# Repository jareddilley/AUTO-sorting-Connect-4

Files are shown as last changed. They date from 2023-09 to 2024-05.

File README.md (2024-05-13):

# AUTO-Sorting-Connect-4
[Arduino Blog](https://blog.arduino.cc/2023/09/27/automating-connect-four-setup-and-cleanup/?queryID=undefined)



Fully 3D printed Connect 4 add-on that sorts the pieces for you at the touch of a button.
The solution is made up of 3 parts which will be broken down below: sensing color, dividing pieces, and one-row handling.

Attached is the Fusion 360 so the models can be edited directly and used to better understand how it is broken down. A YouTube link for the build process and comedic relief: https://www.youtube.com/watch?v=7tsY3SJziWs&t=1s

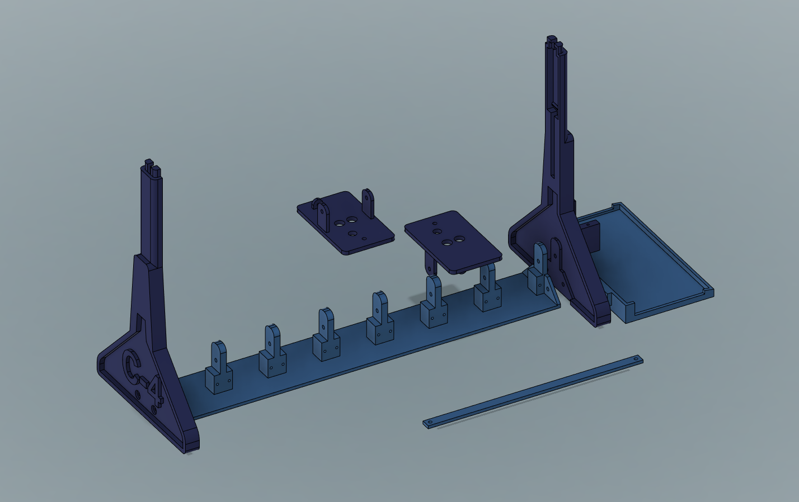
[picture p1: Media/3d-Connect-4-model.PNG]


Below is the full Arduino schematic for anyone trying to build the project. For those who want a closer look, the diagram can be found in the Fritzing Schematic folder. If there are any confusions feel free to ask in the discussion. (don't forget to leave slack in the wires for the platform of the lever to go all the way up and down)

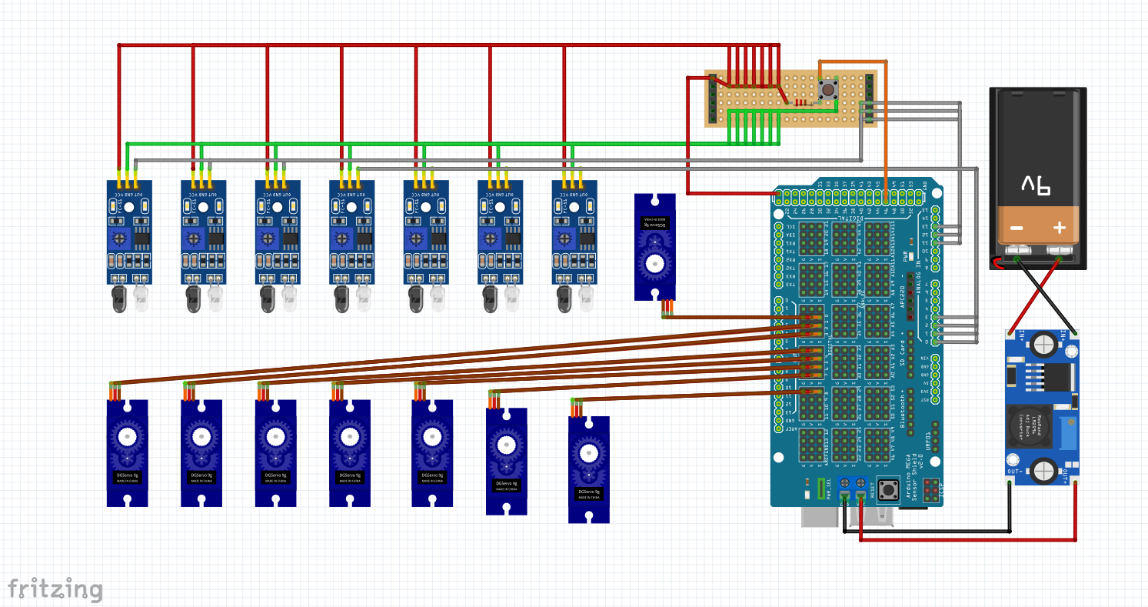
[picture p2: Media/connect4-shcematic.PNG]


# Sensing Color


The IR sensor is able to reflect and receive off of the red piece but not the black piece allowing for a simple binary approach. This requires that one of the piece colors be black, but this method reduces the number of cables and is the simple solution. The most compact place for the sensors, which also does not block the view of the gameplay, ends up being the bottom; we can combine them with the levers that push the pieces to one side or the other.

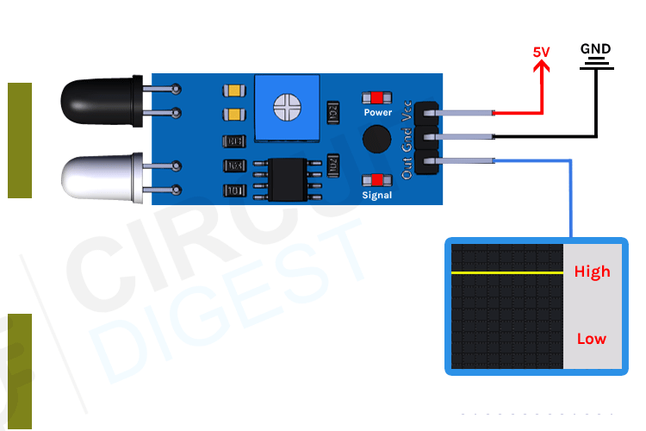
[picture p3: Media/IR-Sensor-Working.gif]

# Dividing Peices


A lever system (think seesaw) is used to push the pieces to one side or the other. A server with a simple linkage is used to tilt the single-point mounted platform to one side or the other letting gravity do the rest. This system is not the most robust approach and has its flaws but is a solution to the problem and can be improved upon. The platform must stop in the middle of each row drop to sense the color before picking a side.
# One Row Handling
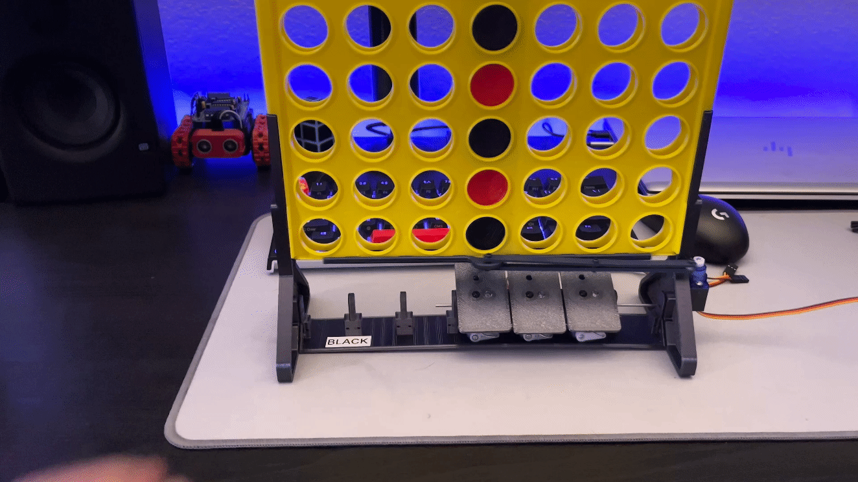
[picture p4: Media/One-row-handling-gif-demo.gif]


The pieces traditionally come out of the bottom so we can use the existing slider to drop the pieces one at a time using a precise servo. The servo can be mounted to the side support and can provide an action that is quick and precise enough to consistently only drop one row at a time. This works under the load of one row or all six.

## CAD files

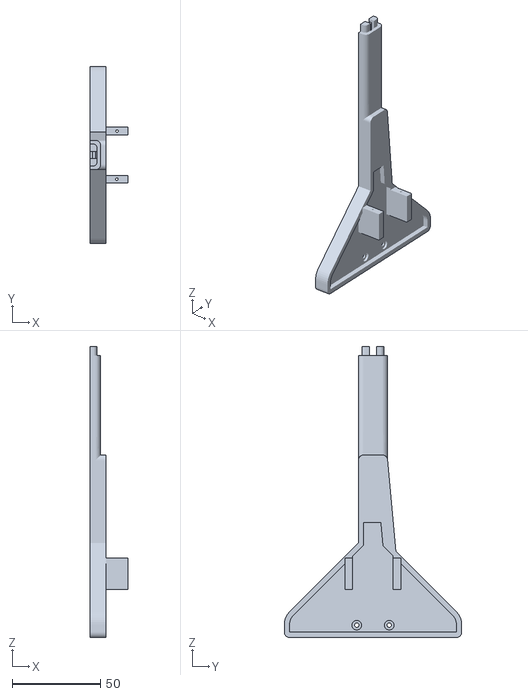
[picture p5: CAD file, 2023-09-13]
STL files/servo_side_support.stl
21.6 x 100.6 x 165.0

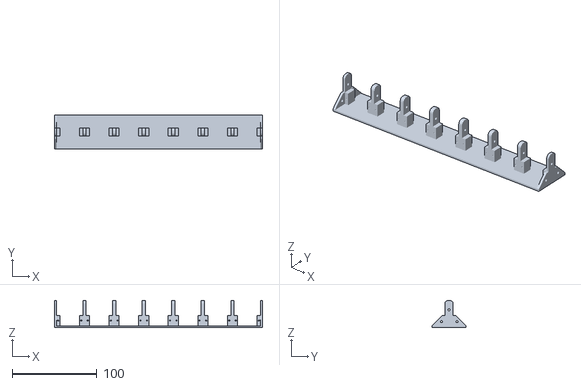
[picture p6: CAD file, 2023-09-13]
STL files/base_X7.stl
246.0 x 40.0 x 32.0

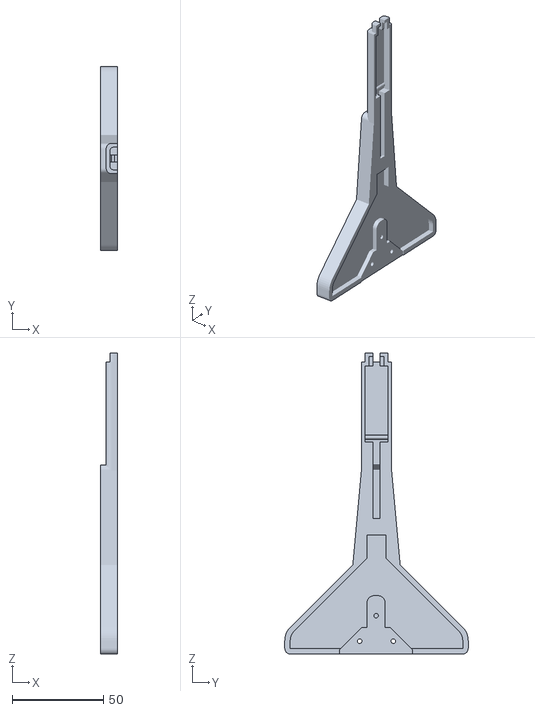
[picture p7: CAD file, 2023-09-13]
STL files/side_support.stl
9.10 x 100.6 x 165.0

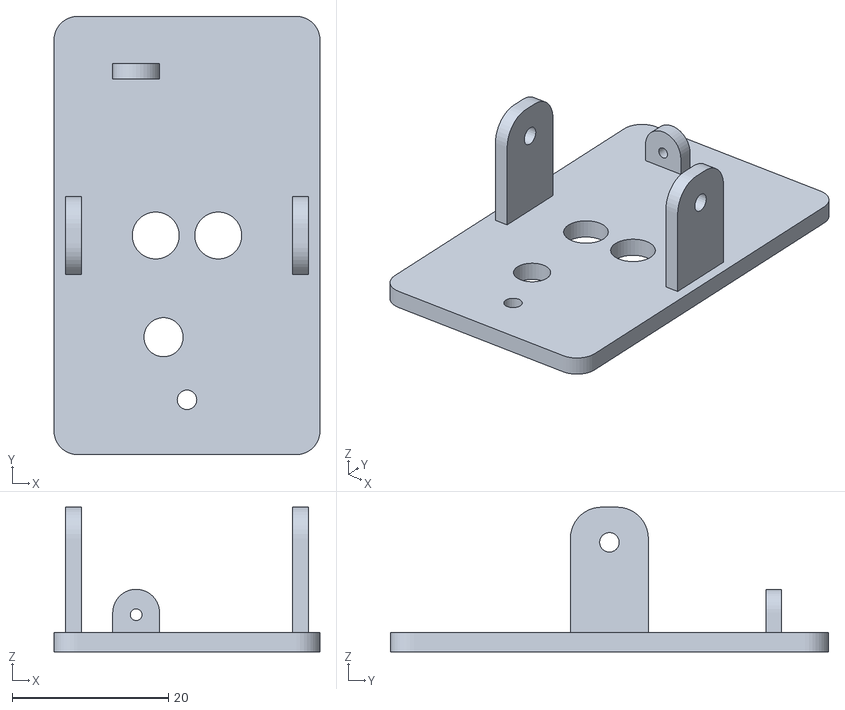
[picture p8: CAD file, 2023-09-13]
STL files/tilt_platform.stl
34.0 x 56.0 x 18.5

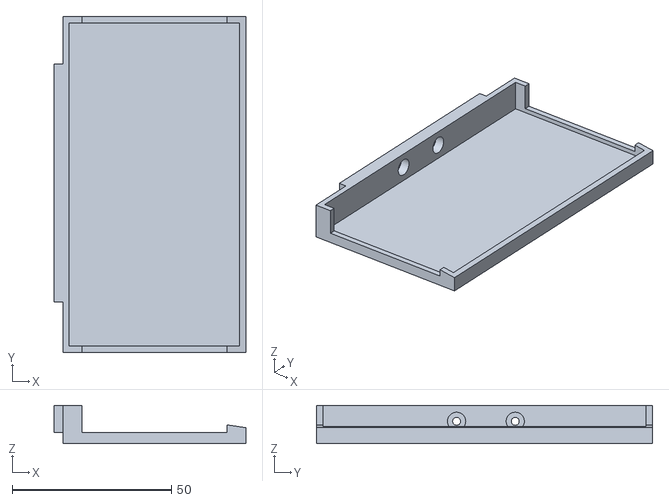
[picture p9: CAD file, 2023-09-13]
STL files/circuit_box.stl
60.2 x 105.5 x 12.0

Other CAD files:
Fusion 360/Sorting Connect 4 Fusion 360.f3d

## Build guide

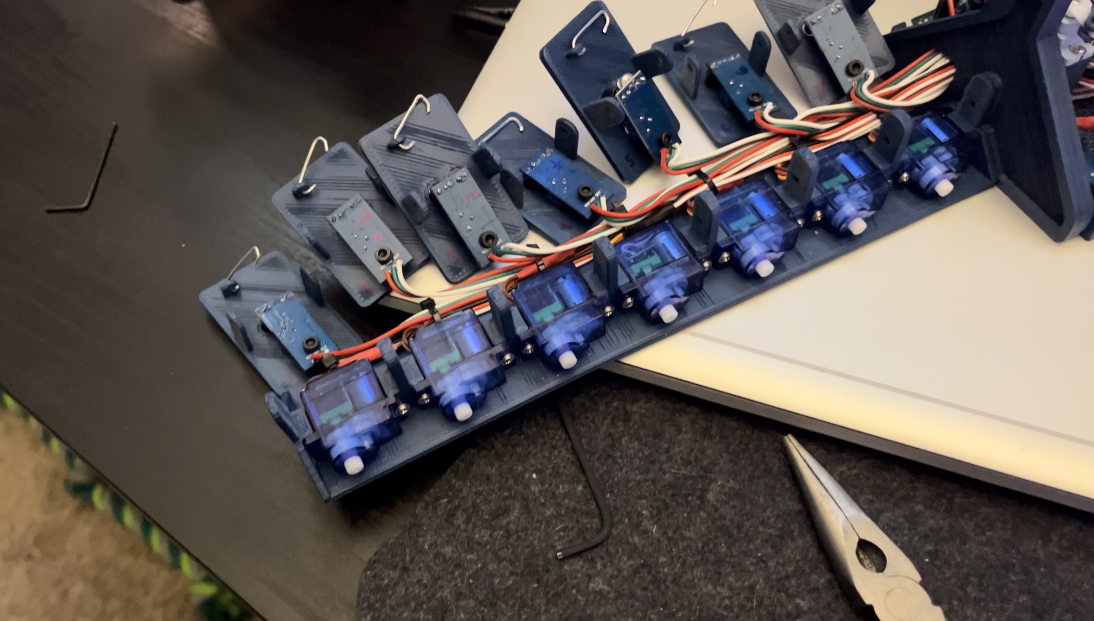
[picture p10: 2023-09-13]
Media/Disassembled-view.jpg

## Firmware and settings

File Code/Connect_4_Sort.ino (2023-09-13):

#include <Wire.h>
#include <Adafruit_PWMServoDriver.h>

// called this way, it uses the default address 0x40
Adafruit_PWMServoDriver pwm = Adafruit_PWMServoDriver();

#define SERVOMIN  100 // this is the 'minimum' pulse length count (out of 4096) 0 degrees
#define SERVOMAX  350 // this is the 'maximum' pulse length count (out of 4096) 90 degrees
#define SERVOMID1  170 // adjustable middle angle
#define SERVOMID2  167
#define SERVOMID3  160
#define SERVOMID4  160
#define SERVOMID5  160 
#define SERVOMID6  180
#define SERVOMID7  180

#define dropServo 0
#define tiltServo1 1 // farthest servo
#define tiltServo2 2
#define tiltServo3 3
#define tiltServo4 4
#define tiltServo5 5
#define tiltServo6 6
#define tiltServo7 7

#define LED_PIN_1 9
#define LED_PIN_2 10
#define buttonPin 46

int currentState = 0;

void setup() {
  pwm.begin();
  pinMode(buttonPin, INPUT);  // set up button pin
  //pinMode(LED_PIN_1, OUTPUT); // set up LED pins
  //pinMode(LED_PIN_2, OUTPUT);
  pwm.setPWMFreq(60);  // Analog servos run at ~60 Hz updates
  pwm.setPWM(tiltServo1, 0, SERVOMID1); // Set Tilt servos to middle
  pwm.setPWM(tiltServo2, 0, SERVOMID2);
  pwm.setPWM(tiltServo3, 0, SERVOMID3);
  pwm.setPWM(tiltServo4, 0, SERVOMID4);
  pwm.setPWM(tiltServo5, 0, SERVOMID5);
  pwm.setPWM(tiltServo6, 0, SERVOMID6);
  pwm.setPWM(tiltServo7, 0, SERVOMID7);
  pwm.setPWM(dropServo, 0, SERVOMIN); // Set Drop servo to closed
  Serial.begin(9600); // start Serial Print
}


void loop() {
  delay(1);
  currentState = digitalRead(buttonPin);
  //digitalWrite(LED_PIN_1, LOW);
  //digitalWrite(LED_PIN_2, HIGH);
  pwm.setPWM(tiltServo1, 0, SERVOMID1);
  pwm.setPWM(tiltServo2, 0, SERVOMID2);
  pwm.setPWM(tiltServo3, 0, SERVOMID3);
  pwm.setPWM(tiltServo4, 0, SERVOMID4);
  pwm.setPWM(tiltServo5, 0, SERVOMID5);
  pwm.setPWM(tiltServo6, 0, SERVOMID6);
  pwm.setPWM(tiltServo7, 0, SERVOMID7);
  if(currentState == HIGH){ // clicked 
    Serial.println("clicked");
    //digitalWrite(LED_PIN_1, HIGH);
    //digitalWrite(LED_PIN_2, LOW);
    for (int i=0; i<6; i++) {
      // Set platform middle for read
      pwm.setPWM(tiltServo1, 0, SERVOMID1);
      pwm.setPWM(tiltServo2, 0, SERVOMID2);
      pwm.setPWM(tiltServo3, 0, SERVOMID3);
      pwm.setPWM(tiltServo4, 0, SERVOMID4);
      pwm.setPWM(tiltServo5, 0, SERVOMID5);
      pwm.setPWM(tiltServo6, 0, SERVOMID6);
      pwm.setPWM(tiltServo7, 0, SERVOMID7);
      delay(300); // was 500
      // Read and print IR sensor value
      int sensorValue1 = analogRead(A0); //
      int sensorValue2 = analogRead(A1);
      int sensorValue3 = analogRead(A2);
      int sensorValue4 = analogRead(A3);
      int sensorValue5 = analogRead(A13);
      int sensorValue6 = analogRead(A12);
      int sensorValue7 = analogRead(A11);
      // Print incoming values
      Serial.print("sensor1: ");
      Serial.println(sensorValue1);
      Serial.print("sensor2: ");      
      Serial.println(sensorValue2);
      Serial.print("sensor3: ");
      Serial.println(sensorValue3);
      Serial.print("sensor4: ");
      Serial.println(sensorValue4);
      Serial.print("sensor5: ");
      Serial.println(sensorValue5);
      Serial.print("sensor6: ");
      Serial.println(sensorValue6);
      Serial.print("sensor7: ");
      Serial.println(sensorValue7);
      //Serial.print("A3: ");
      //Serial.println(analogRead(A3));
      delay(300); // was 500
      // Tilt platform based on RED or BLACK piece
      if(sensorValue1 < 500){ // BLACK (did not reflect IR signal) 
        pwm.setPWM(tiltServo1, 0, SERVOMAX-10);
      }else{  // RED (reflected IR signal)
        pwm.setPWM(tiltServo1, 0, SERVOMIN-20);
      }
      if(sensorValue2 < 500){ // BLACK (did not reflect IR signal) 
        pwm.setPWM(tiltServo2, 0, SERVOMAX-10);
      }else{  // RED (reflected IR signal)
        pwm.setPWM(tiltServo2, 0, SERVOMIN-25);
      }
      if(sensorValue3 < 500){ // BLACK (did not reflect IR signal) 
        pwm.setPWM(tiltServo3, 0, SERVOMAX-10);
      }else{  // RED (reflected IR signal)
        pwm.setPWM(tiltServo3, 0, SERVOMIN-10);
      }
      if(sensorValue4 < 500){ // BLACK (did not reflect IR signal) 
        pwm.setPWM(tiltServo4, 0, SERVOMAX-20);
      }else{  // RED (reflected IR signal)
        pwm.setPWM(tiltServo4, 0, SERVOMIN-10);
      }
      if(sensorValue5 < 500){ // BLACK (did not reflect IR signal) 
        pwm.setPWM(tiltServo5, 0, SERVOMAX);
      }else{  // RED (reflected IR signal)
        pwm.setPWM(tiltServo5, 0, SERVOMIN-20);
      }
      if(sensorValue6 < 500){ // BLACK (did not reflect IR signal) 
        pwm.setPWM(tiltServo6, 0, SERVOMAX);
      }else{  // RED (reflected IR signal)
        pwm.setPWM(tiltServo6, 0, SERVOMIN-15);
      }
      if(sensorValue7 < 500){ // BLACK (did not reflect IR signal) 
        pwm.setPWM(tiltServo7, 0, SERVOMAX);
      }else{  // RED (reflected IR signal)
        pwm.setPWM(tiltServo7, 0, SERVOMIN+10);
      }
      delay(150);
      // Drop a single Row
      pwm.setPWM(dropServo, 0, SERVOMAX);
      delay(125); // drop speed
      pwm.setPWM(dropServo, 0, SERVOMIN);
      delay(500); // was 500 ms
    }
  }
}
